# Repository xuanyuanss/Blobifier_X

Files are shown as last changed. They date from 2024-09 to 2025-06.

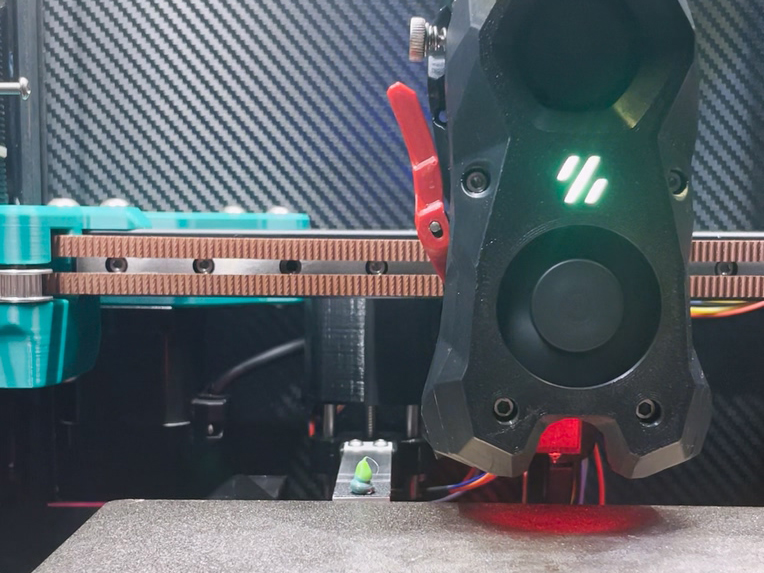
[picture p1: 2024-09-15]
Assets/实物图1.jpg

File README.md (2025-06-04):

# 已更新至V2版本，结构和程序均完成了大更新！！！
## [V2版本链接](https://github.com/xuanyuanss/Blobifier_X-V2) https://github.com/xuanyuanss/Blobifier_X-V2

# Blobifier_X
## A variant of Blobifier--No need for a lifting gantry

Although its physical structure is completely different from Blobifier, it only refers to its nozzle flushing idea, while making targeted modifications in the software part. For the original Blobifier, please go here [Blobifier](https://github.com/Dendrowen/Blobifier).

The original Blobifier is not friendly to Voron2.4, requiring frequent lifting of the gantry, sacrificing the effective printing area of the heated bed, and there may be a risk of the print head hitting the model. Therefore, I designed Blobifier_X.

Blobifier_X is installed on the gantry, and it does not need to lower the gantry during flushing. Instead, a small stepper motor is used to achieve the lifting of the tray to facilitate blob formation.

[中文说明在Makerworld](https://makerworld.com.cn/zh/models/448667#profileId-366651)。

实物图1
实物图2
示意图 (2)
示意图 (5)
示意图 (8)
示意图 (1)

# Update Description:
## 2024年9月1日
Adjust the blob ejection logic: The last blob of the current flush is ejected when the next flush stops, that is, the printing is restored immediately after the flush ends, without waiting for the Blobifier_X to return to its position, which effectively reduces the overflow of nozzle consumables. Even without a wiping mouth, the wiping tower/heated bed is also very clean.

# Bill of Materials:
* 28BYJ-48 stepper motor x1,
* TMC2209 or other drivers x1,
* ∅5x50 cylindrical pin x2,
* T5 lead screw with nut, length 40 x1,
* D2F-01L micro switch x1,
* M3x4x5 heat melt nut x8,
* M3x3 set screw x4, can also be used on BMG,
* M3x10 round head hex nut x4,
* M3x12 round head hex nut x2,
* M3x16 round head hex nut x1,15x2x75 aluminum bar x1, I used CNC TAP, the length of the aluminum bar may not be suitable for you, please adjust it yourself to extend 4-5mm in front of the nozzle, punch holes according to the figure below.
* Heated bed film 15x15mm x1, textured film, adhesive on the back, about 0.4 thickness, there are many on TB, generally black, buy the smallest specification and cut it yourself.

托盘

# Key Assembly Steps Description:
* When pressing the coupler into the heat melt nut, it is recommended to assemble it with the motor and lead screw first, then press the nut in, 和 press the nut to the bottom.
* Cut the motor shaft perpendicular to its wiring direction, 和 pre-assemble it with the main body and cylindrical pin in advance;
* Assemble the lead screw, nut, coupler, 和 slider into a whole;
* Then assemble the above two parts together, tighten the set screw at the end of the motor shaft, at this time, you may need to use pliers to rotate the lead screw so that the two corresponding set screws can be tightened.
* Finally, assemble the remaining parts, 和 don't forget to install the bump block on the print head.

# Regarding motor wiring and driver instructions:
28BYJ-48 is a 5-line 4-phase motor, do not connect the red wire when wiring, and connect the other 4 wires according to the two-phase motor wiring.
The voltage used by 28BYJ-48 is 5V, you need to cut the Vin (VM) pin of the driver, and lead out a line to connect to 5V.


28BYJ-48

# Tuning Instructions:
* Upload Blobifier_X to the printer, 和 include the blobifier_x.cfg file in printer.cfg, modify the motor and limit pin feet in blobifier_x_hw.cfg.
* Important: Motor direction debugging, manually place the slider in the middle of its travel, run MANUAL_STEPPER STEPPER=blobifier_x MOVE=5 (the motor moves a short distance, such as 5), at this time, the slider should move down (that is, away from the motor direction), if the movement is opposite, please adjust the motor running direction.
* Slider zero position adjustment: Adjust the micro switch impact screw on the slider (M3x16), so that when the micro switch is triggered, there is some gap between the slider and the main body (for example, 1mm, the gap size is not strictly required, to avoid the slider hitting the Blobifier_X main body when returning to zero). Install Blobifier_X on the printer, run MANUAL_STEPPER STEPPER=blobifier_x MOVE=5, so that the slider moves away from the micro switch, and then run BLOBIFIER_HOME, at this time, the slider should move up and stop when the micro switch is triggered, at this time, move the print head close to the tray (be careful of collision, you can move the print head manually), and observe its distance from the tray. This is a repetitive process, use MANUAL_STEPPER STEPPER=blobifier_x MOVE=5 and BLOBIFIER_X_HOME commands flexibly and adjust M3x16, so that the tray is about 0.2-0.6mm below the print head. Note: The BLOBIFIER_HOME_X command (accurately said, when the parameter STOP_ON_ENDSTOP=1 in the MANUAL_STEPPER command) needs some time (about a few seconds), at this time, the printer will not execute other commands, please wait patiently.
* Finally, move the print head to the middle of the tray, 和 record the X, Y coordinates (the Y coordinate is generally the maximum travel of the printer Y), fill in the variable_purge_x, variable_purge_y in blobifier_x.cfg; the parameters variable_kick_ready_x, variable_kick_x are the X coordinates where the print head is ready to kick off the blob and after the blob is kicked off, which can be set according to the actual situation, generally respectively Purge_x+20, Purge_x+50.
* The provided configuration files are mainly used in conjunction with ERCF and HAPPY HARE, 和 the specific parameter settings in HAPPY HARE should refer to the HAPPY HARE and BLOBIFIER documents.

# Printing Suggestions:
* Appropriately increase the number of outer walls and top and bottom surfaces to give Blobifier_X enough strength.
* Keep the cylindrical pin installation holes of the main body and slider in the same direction to ensure that they have the same size accuracy as much as possible.
* If the slider is too tight, you can appropriately enlarge the hole with a drill, but don't be too loose, so that Blobifier_X has good rigidity and can slide smoothly, it is recommended to apply some low-viscosity grease.
* The slider CAD file is provided, which can be modified according to your own situation.
* Two types of bump blocks are provided, 和 the V2 version is closer to the heated bed, avoiding the problem of not being able to kick off when the blob is small.
* The provided material bucket CAD file is only suitable for my own printer, mainly for your reference, 和 can be modified or designed by yourself.

# Finally:
* At present, there is no perfect solution for waste material processing of VORON2 structure printers, 和 the current plan basically meets the usage. As the printing progresses, the gantry gradually rises, and there is basically no risk of Blobifier_X hitting the waste material.
* Thank the Blobifier open source project, the author's creativity is really great.

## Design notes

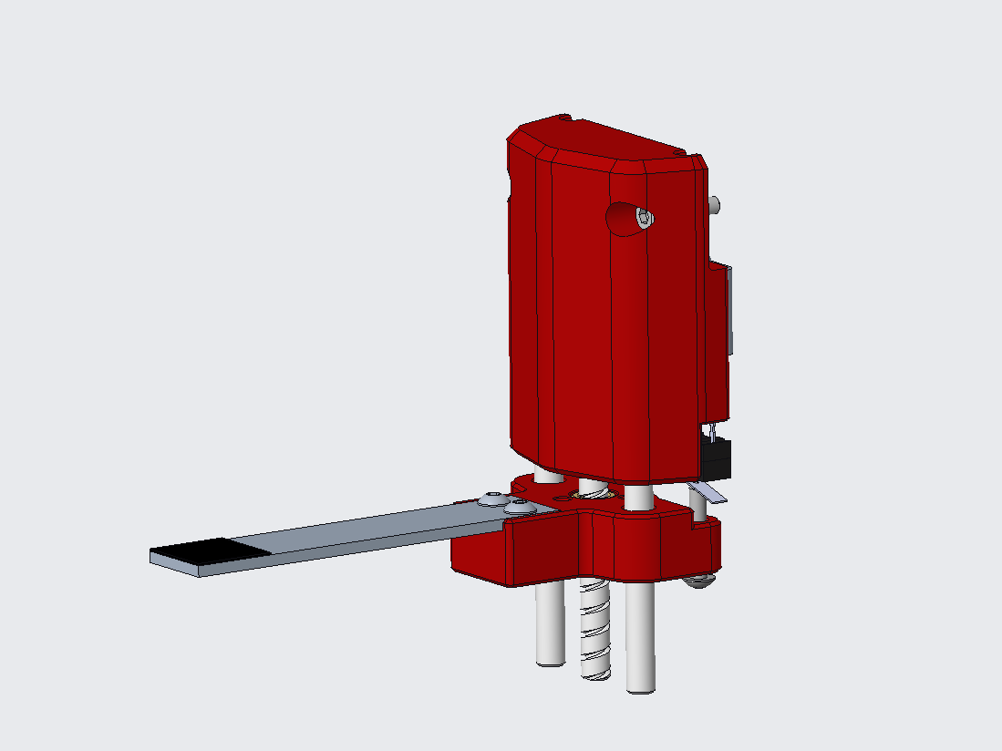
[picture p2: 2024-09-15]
Assets/示意图 (6).png

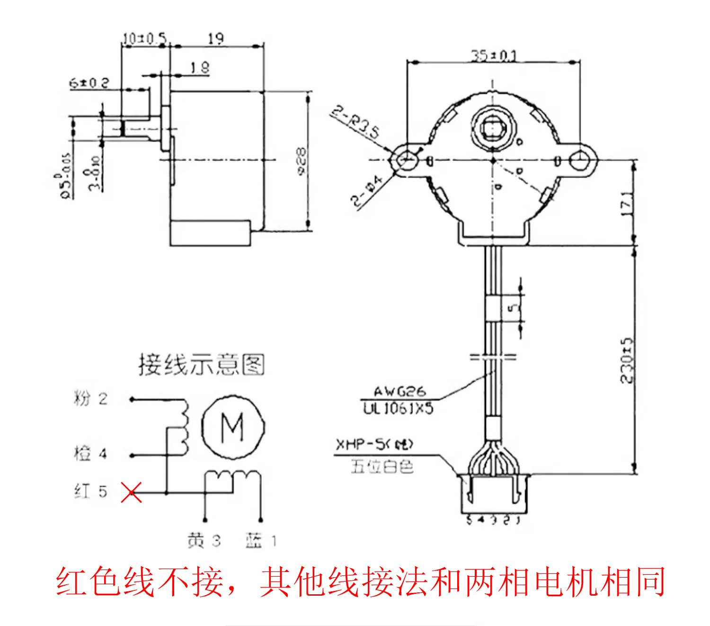
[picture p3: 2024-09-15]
Assets/28BYJ-48.jpg

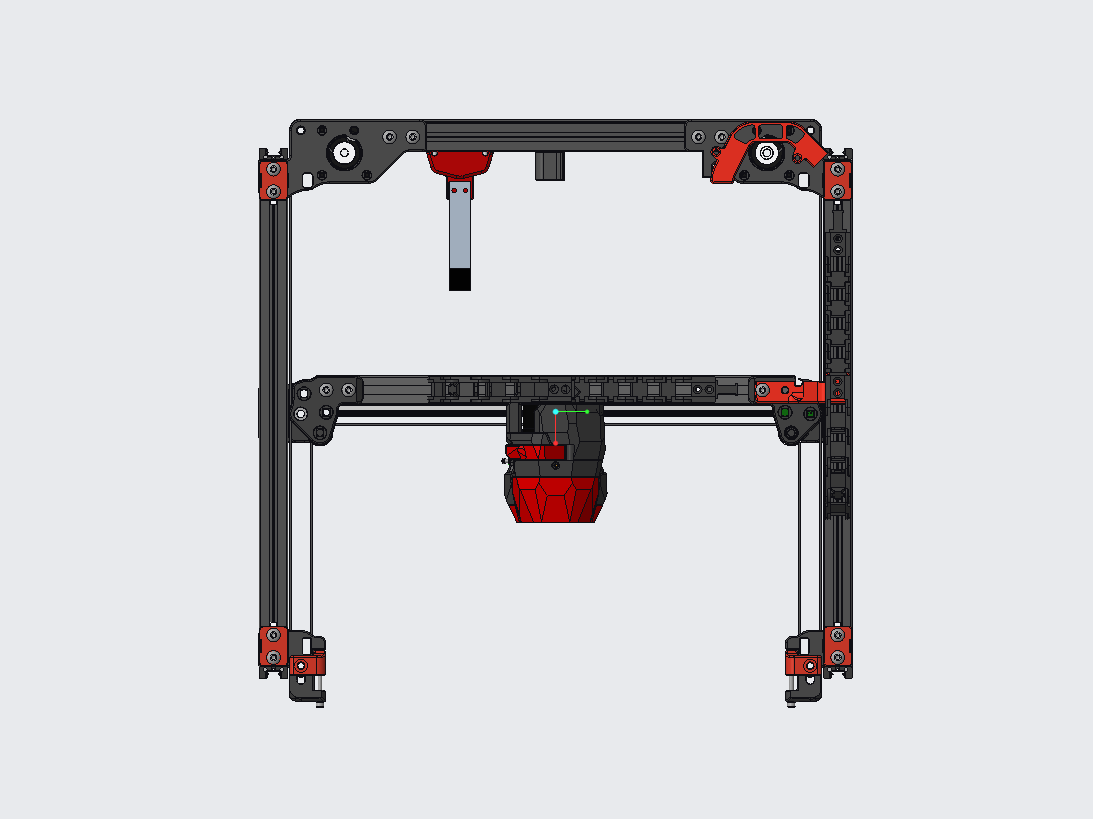
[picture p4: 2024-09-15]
Assets/示意图 (3).png

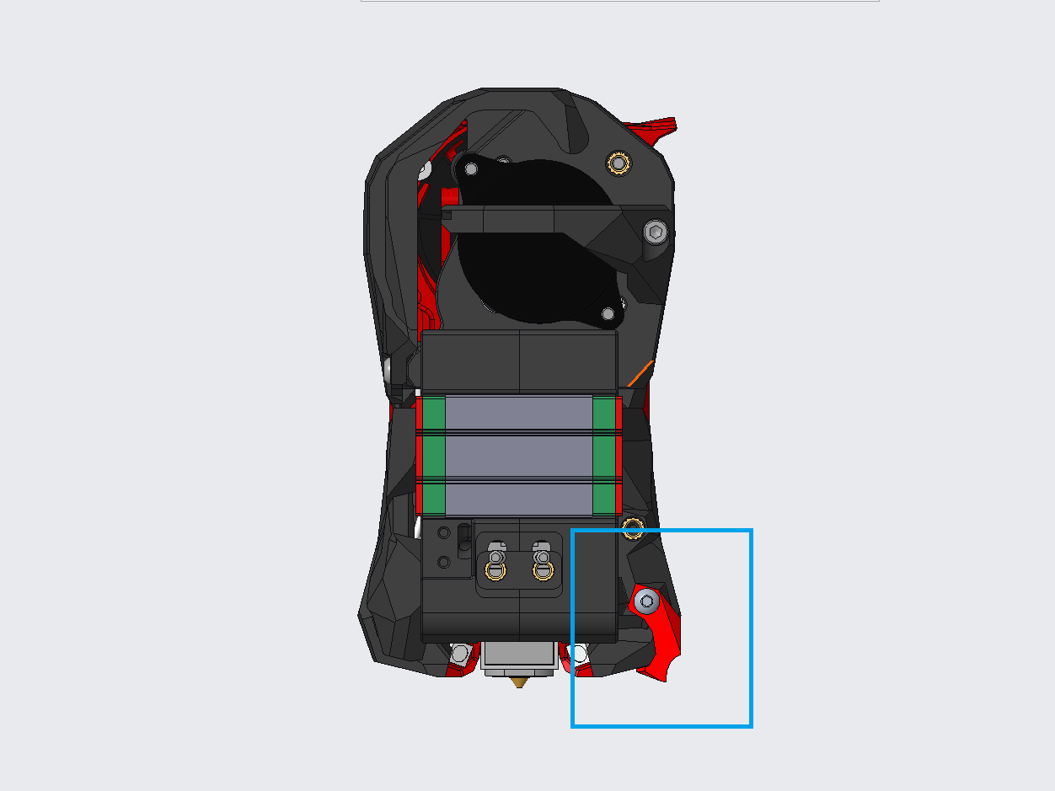
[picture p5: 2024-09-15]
Assets/示意图 (1).png

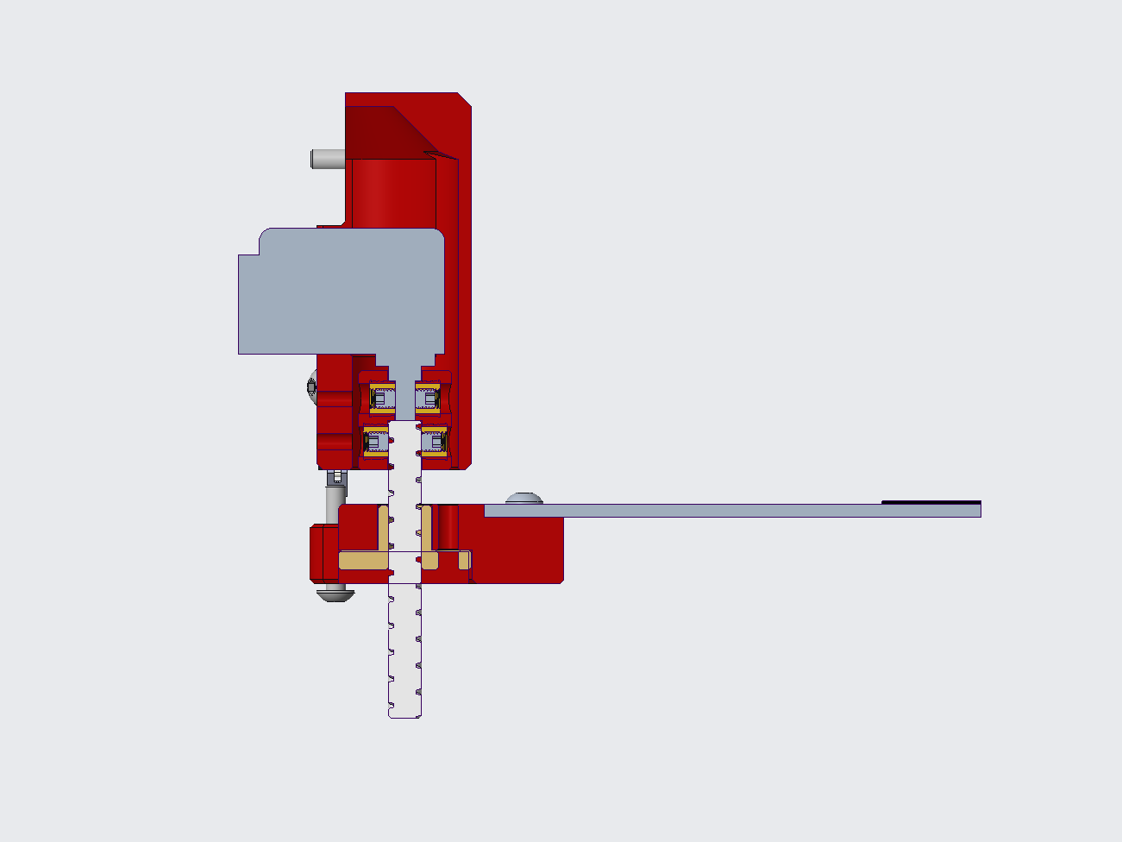
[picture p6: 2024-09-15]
Assets/示意图 (8).png

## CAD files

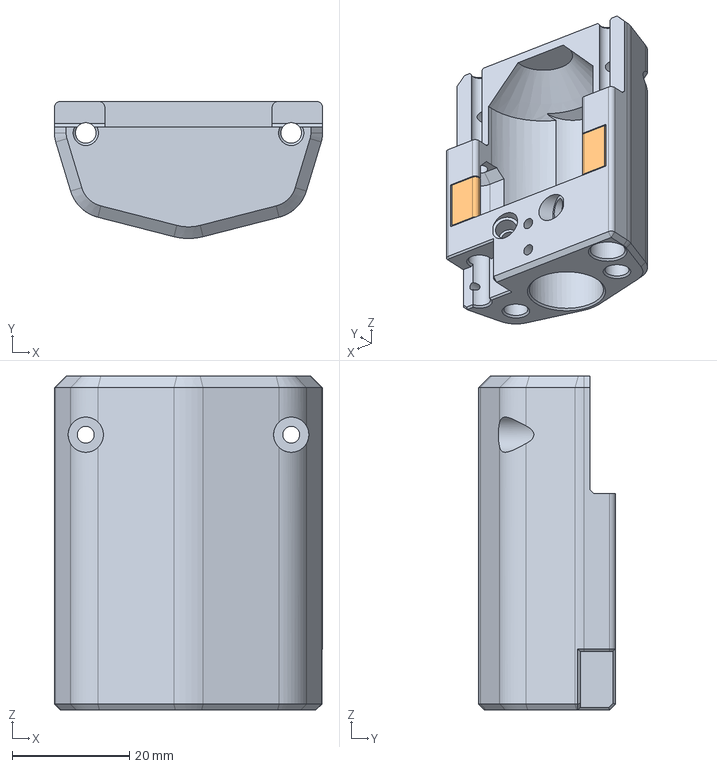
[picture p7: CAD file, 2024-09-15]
CAD/主体.step
45.7 x 23.3 x 56.9 mm

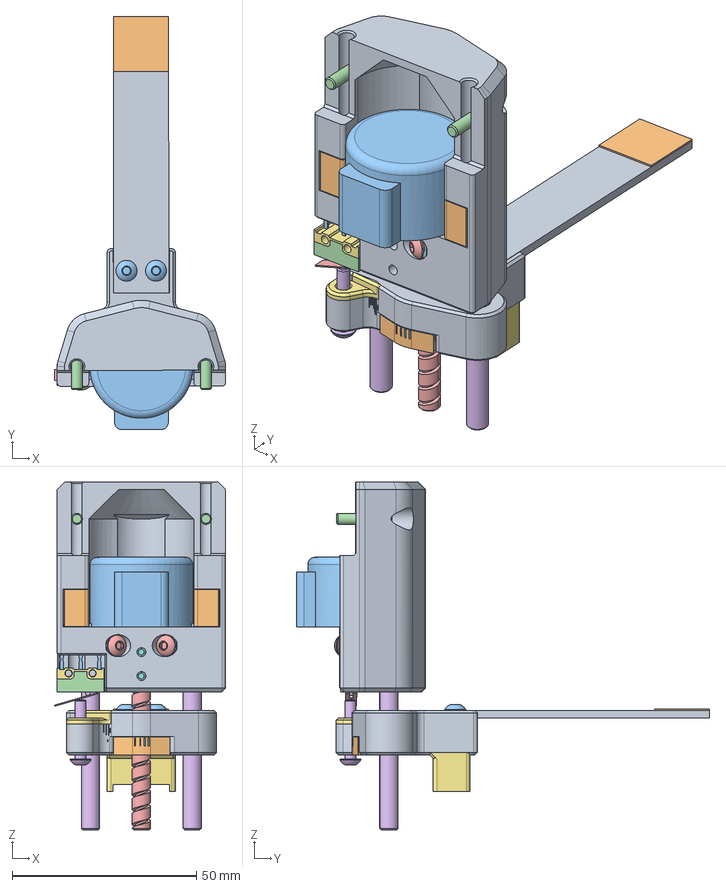
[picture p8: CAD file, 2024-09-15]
CAD/blobifier_x.step
46.5 x 112.1 x 94.4 mm
28BYJ_48
COUPLING
LEAD_SCREW
PIN_SHAFT x 2
SLIDER
NUT
SLIDER_V2
BOSS-EXTRUDE3_2_
BOSS-EXTRUDE2
BOSS-EXTRUDE3_1_
BOSS-EXTRUDE3_3_
CUT-EXTRUDE2
BOSS-EXTRUDE4
CUT-EXTRUDE1
NUT_M3X4X5 x 10
M3X10 x 2
M3X12 x 2
M3X1200 x 2
M3X1600
M3X8 x 2
M3X30001 x 4

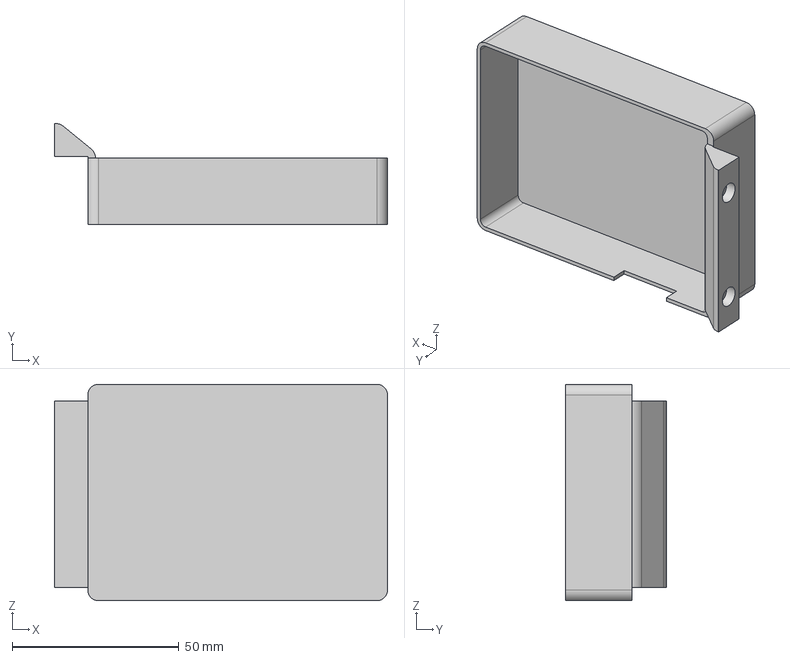
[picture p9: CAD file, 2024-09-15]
CAD/料桶2.step
100.0 x 30.4 x 65.0 mm

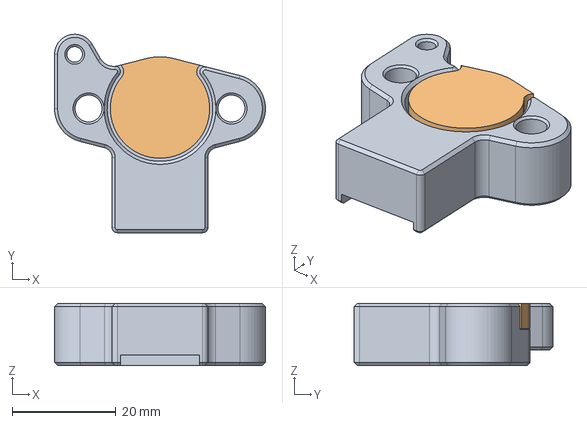
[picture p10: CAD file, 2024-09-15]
CAD/滑块_v2.step
40.8 x 38.3 x 12.0 mm

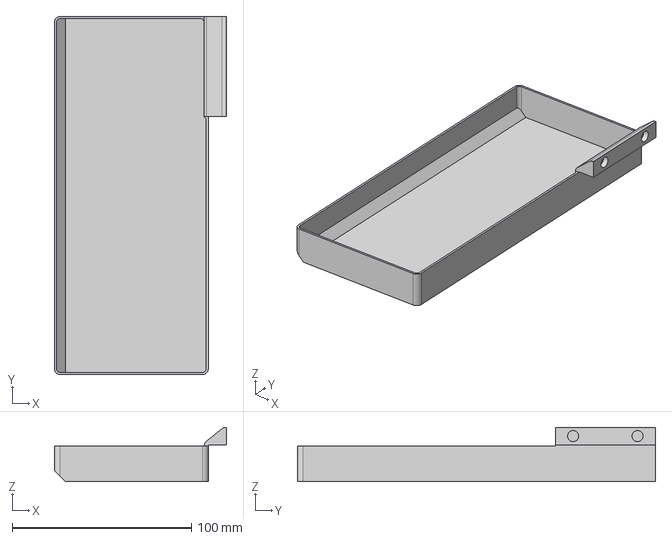
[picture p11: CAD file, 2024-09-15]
CAD/料桶1.step
96.2 x 200.0 x 30.4 mm

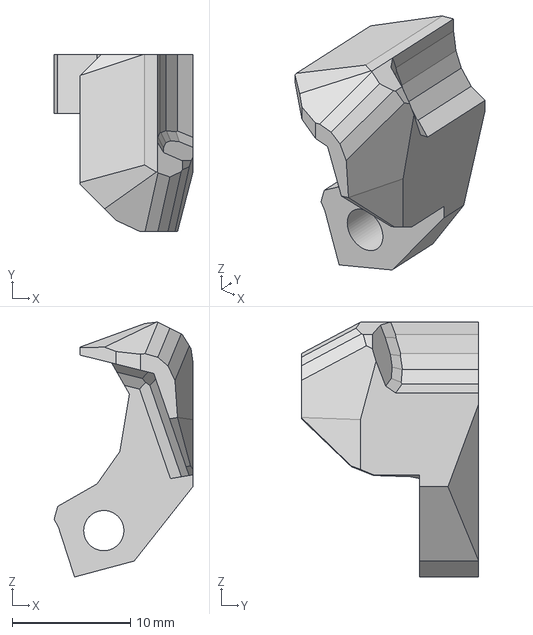
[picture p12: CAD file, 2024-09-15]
CAD/撞块_V3.step
11.7 x 15.0 x 21.6 mm

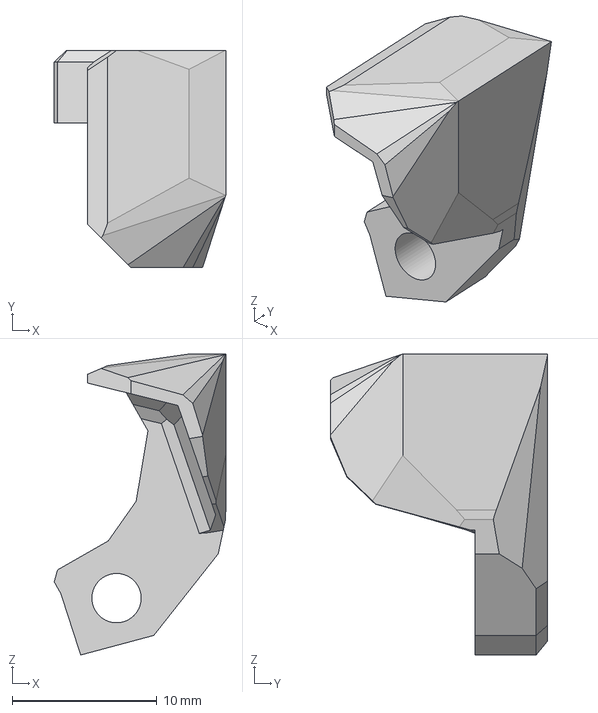
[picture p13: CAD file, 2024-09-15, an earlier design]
CAD/撞块_V1.step
11.8 x 15.0 x 20.8 mm

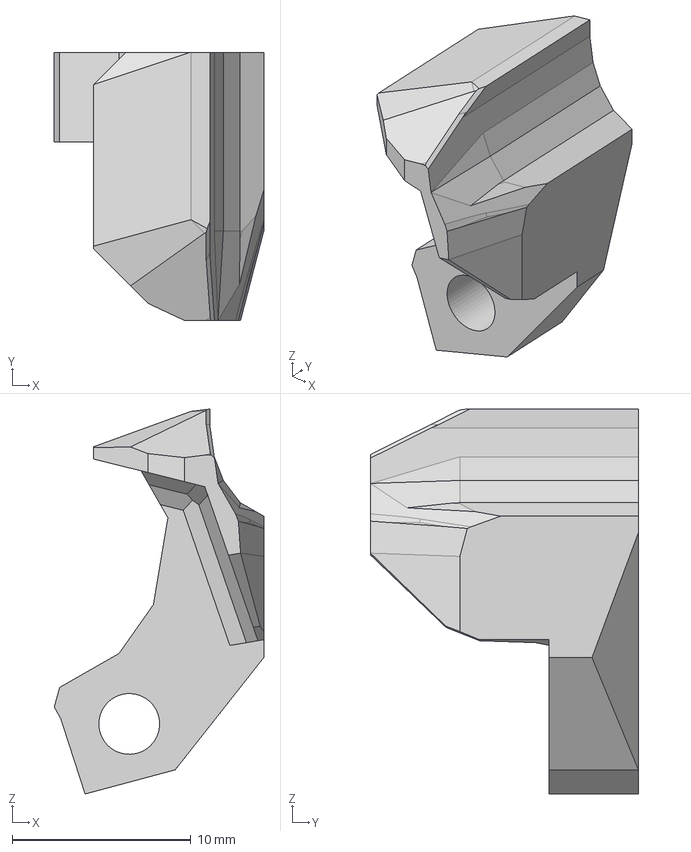
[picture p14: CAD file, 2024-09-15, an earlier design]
CAD/撞块_V2.step
11.7 x 15.0 x 21.6 mm

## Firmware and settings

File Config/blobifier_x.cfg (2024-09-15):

######################## Blobifier_X ########################

########################### 声明 ############################
# Blobifier_X是Blobifier的一个变体（X-MEN？，No *＾-＾*），是一个用于多色打印的喷嘴排除废料的项目，适配于Voron2.4等龙门移动式3D打印机。具备以下功能：
# 1.可用于单热端多色打印换料后耗材冲刷，可省掉擦料塔，但建议使用很小的擦料塔以清理喷嘴溢出的耗材。
# 2.本配置文件主要是配合ERCF和HAPPY HARE使用，HAPPY HARE中具体参数配置请参考HAPPY HARE及BLOBIFIER文档。
# 3.使用本想目前，请您确保了解本项目的、工作过程，避免对打印机造成意外损害。如不慎产生意外损失，开发人员不承担任何责任。

# 其实Blobifier_X物理结构已与Blobifier完全不同，仅是参考了其喷嘴冲刷创意，同时在软件部分做针对性修改，原版Blobifier请移步https://github.com/Dendrowen/Blobifier。
# 原版Blobifier对voron2.4并不友好，需要频繁升降龙门，并且牺牲热床有效打印面积，同时可能存在打印头撞击模型的风险。所以我设计了Blobifier_X。
# Blobifier_X安装在龙门上，冲刷时不需要降低龙门，而是通过一个小的步进电机实现托盘的升降而促使blob成型。

# 目前VORON2结构打印机废料处理尚无完美方案，目前方案基本满足使用，随着打印的进行，龙门逐渐升高，基本不会出现Blobifier_X撞击废料的风险。
# 感谢Blobifier开源项目，作者的创意真的很棒。

# 感谢您选择本项目，祝您生活愉快！

#！！！本宏中保留了一些利用铜刷清洁喷嘴的代码，但未启用，亦未调试，给那些想使用清洁刷的朋友使用，但请自行配置调试，切记切记！！！

# 轩辕十四
# 2024.8.17
##########################################################################################
##########################################################################################

# Blobifier_X硬件配置文件
[include blobifier_x_hw.cfg]

##########################################################################################
[gcode_macro BLOBIFIER_X]
# 这些参数定义了您的丝材清洗。回抽变量用于在清洗后立即回抽，以防止不必要的渗漏。一些丝材特别容易渗漏，可能在回抽后一两秒内继续从喷嘴渗出。根据需要更新。
variable_purge_spd:                      400    # 清洗速度：400毫米/分钟。
variable_purge_temp_min:                 200    # 最低喷嘴清洗温度：200摄氏度。
variable_retract_before_park:            2.0    # 清洗前回抽量：2.0毫米（设置为0以禁用）。
variable_retract_before_resume:          1.0    # 恢复打印前前回抽量，减少喷嘴溢出：1.0毫米（设置为0以禁用）。
variable_retract_speed:                 2000    # 回抽速度：2000毫米/分钟。

# 这些参数定义了您的擦洗次数、移动速度、安全Z轴间隙以及您想要擦洗的次数。根据需要更新。

#variable_wipe_qty:                         2    # Number of complete (A complete wipe: left, right, left OR right, left, right) wipes.
variable_travel_spd_xy:                10000    # X和Y轴上的移动速度（非清洗）：10000毫米/分钟。
variable_blob_kick_spd:                10000    # 将残留物踢开的速度：10000毫米/分钟。
#variable_wipe_spd_xy:                  15000    # Nozzle wipe speed in mm/min.


# These parameters define the size of the brush. Update as necessary. A visual reference 
# is provided below.
# 
#                  ?   brush_width   ?                            
#                   _________________                                                          
#                  |                 |  ?                Y position is acquired from your 
#  brush_start (x) |                 | brush_depth       stepper_y position_max. Adjust 
#                  |_________________|  ?                your brush physically in Y so 
#                          (y)                           that the nozzle scrubs within the 
#                      brush_front                       brush.                                              
# __________________________________________________________
#                     PRINTER FRONT
# 
# 
# Start location of the brush. Defaults for 250, 300 and 350mm are provided below. 
# Uncomment as necessary
# The brush will move diagonally through teh brush.
#    from (brush_start,brush_min_y) to (brush_start + brush_width, Y max)
#variable_brush_start:                    34    # For 250mm build    
#variable_brush_start:                    83.5  # For 300mm build
#variable_brush_start:                     37.5   #43.5   #82    # for 350mm build    GNEU
#variable_brush_min_y:                    353    # Minimum position in Y of the brush. 
#variable_brush_width:                     32    # width of the brush
#variable_position_wiper:                  85.5  # mid point of the wiper

# 冲刷位置，即喷嘴置于托盘中心时喷嘴的坐标
variable_purge_x:                          60     #X坐标
variable_purge_y:                          249    #Y坐标，通常为Y最大行程
variable_kick_x:                           80     #踢除blob后X坐标
variable_kick_ready_x:                     110    #准备踢除blob时X坐标
variable_yield_y:                          198    #打印头避让blob，调整此值使打印头底部与托盘距离少于15mm的部位避开即可，避免不正确的撞击blob，用于下次停靠时敲击blob

##########################################################################################
# BLOB TUNING
#
# 下一节定义了如何执行清洗序列。这是您调整清洗以创建漂亮残留物的地方。请参阅视觉参考以获得更好的理解。视觉参考中填充了示例值。以下是一些有助于调整的指南。
#
#                          \_____________/
#                             |___|___|
#                                \_/            ______________  < End of third iteration.
#                                / \                                  HEIGHT:   3 x iteration_z_raise - (2 + 1) x iteration_z_change  (3 x 5 - 2 x 1.2 = 11.4)
#                               |   |                                 EXTRUDED: 3 x max_iteration_length                              (3 x 50 = 150)
#                              /     \          ______________  < End of second iteration.
#                             |       \                               HEIGHT:   2 x iteration_z_raise - 1 x iteration_z_change        (2 x 5 - 1 x 1.2 = 8.8)
#                            /         |                              EXTRUDED: 2 x max_iteration_length                              (2 x 50 = 100)
#                           |           \       ______________  < End of first iteration. 
#                          /             \                            HEIGHT:   1 x iteration_z_raise                                 (1 x 5 = 5)
#                         |               |                           EXTRUDED: 1 x max_iteration_length                              (1 x 50 = 50)
#___________               \             /      ______________  < Start height of the nozzle. default value: 1.5mm
#           |_______________\___________/_      ______________  < Bottom of the tray
#           |_____________________________|
#           |
# 
########################### BLOB TUNING ##############################
# +-------------------------------------+----------------------------+
# |  Filament sticks to the nozzle at   | Incr. purge start          |
# |    initial purge (first few mm)     |                            |
# +-------------------------------------+----------------------------+
# |  Filament scoots out from under     | Incr. temperature          |
# |  the nozzle at the first iteration  | Decr. iteration_z_raise    |
# |                                     | Incr. max_iteration_length |
# +-------------------------------------+----------------------------+
# |  Filament scoots out from under the | Decr. purge_spd            |
# |  the nozzle at later iterations     | Incr. iteration_z_change   |
# +-------------------------------------+----------------------------+
# |  Filament sticks to the nozzle at   | Decr. iteration_z_change   |
# |         later iterations            |                            |
# +-------------------------------------+----------------------------+
# |        I think my blobs can         | Balsy... Increase          |
# |          be much bigger!            | max_iterations_per_blob    |
# +-------------------------------------+----------------------------+
#

# 一次迭代中要挤出的丝材的最大毫米数（长度）。一个残留物包含多次迭代。
variable_max_iteration_length:                   40

# 每次迭代托盘下降的量
variable_iteration_bl_move:                       5

# 当喷嘴相对变高且残留物变宽时，需要减少托盘下降量。
variable_iteration_move_change:                      0.7

# 每个残留物的最大迭代次数。3次迭代对于大多数清洗应该足够。如果不够，Blobifier将为单次清洗创建多个残留物。
variable_max_iterations_per_blob:                 3

# 清洗前和清洗后的停留时间（毫秒），以释放喷嘴的压力。
variable_eject_hop:                               2.0

# 清洗前和清洗后的停留时间（毫秒），以释放喷嘴的压力，并使blob冷却。
variable_blob_cooling_time:                    2000

# 设置零件冷却风扇的速度。禁用可以帮助防止喷嘴冷却并刺激流动，启用它可以防止残留物粘在一起。值的范围从0到1，或者如果您不想更改，则为-1。
#variable_part_cooling_fan:                      -1  # Leave it unchanged
#variable_part_cooling_fan:                       0  # Disable the fan
variable_part_cooling_fan:                        1  # Run it at full speed


##########################################################################################
# 清洗长度调整
#
# 当工具映射的purge_volumes或参数PURGE_LENGTH未设置时，使用的默认清洗长度。
variable_purge_length:                          60

# 即使没有更换工具，也要执行的绝对最小清洗长度。
variable_purge_length_minimum:                  30  

# 切片机的值通常有点浪费。在这里调整以获得最优值。1.0是一个好的起点。
variable_purge_length_modifier:                  1.2

# 在清洗体积之后要添加的丝材长度。清洗体积并不总是考虑到刀具，因此从深色到浅色的更换可能足够长，但从浅色到深色可能太短。当您应该更改这个值时：
# 增加：当深色到浅色的更换很好，但浅色到深色的更换不好时。
# 减少：当浅色到深色的更换很好，但深色到浅色的更换不好时。不要忘记增加purge_length_modifier。
variable_purge_length_addition:                 5


gcode:

##########################################################################################
# 记录状态（包括风扇、速度等）
#
  # General state
  SAVE_GCODE_STATE NAME=BLOBIFIER_X_state
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

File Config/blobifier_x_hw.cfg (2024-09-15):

[manual_stepper blobifier_x]
step_pin:   PE1
dir_pin:    PE0
enable_pin: !PC5
microsteps: 4
rotation_distance:4
full_steps_per_rotation: 32
gear_ratio: 64:1
velocity: 1.2
accel: 100
endstop_pin: ^PA0

[tmc2209 manual_stepper blobifier_x]
uart_pin: PD11
#interpolate: True
run_current: 0.4
hold_current: 0.2
#sense_resistor: 0.110
stealthchop_threshold: 0
